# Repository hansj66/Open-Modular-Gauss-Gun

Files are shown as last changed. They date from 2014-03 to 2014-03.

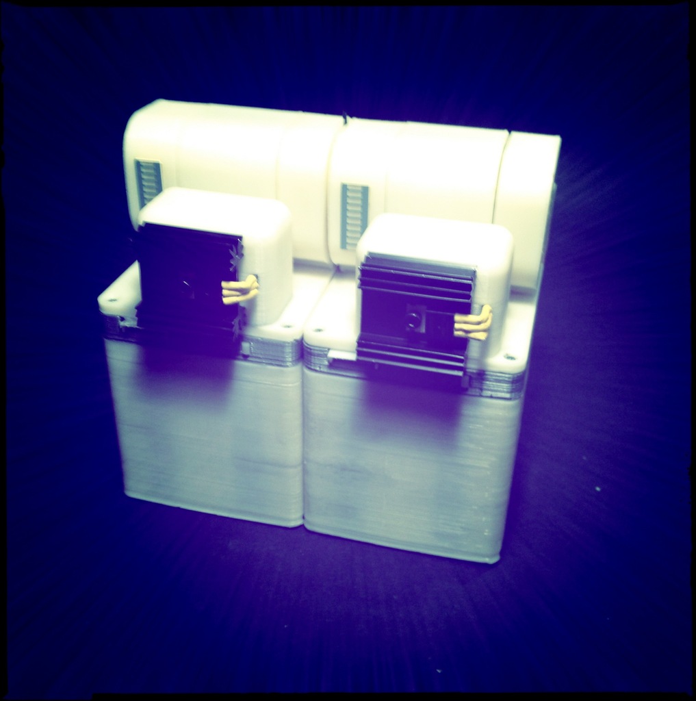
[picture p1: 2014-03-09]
Two_Stages_display_large.jpg

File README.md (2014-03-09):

Open-Modular-Gauss-Gun
======================

Description

A modular electromagnetic accelerator that actually works...;)

Warning: This project involves the use of a capacitor bank that contains more than enough energy to kill you. Do not attempt to build this unless you know what you are doing ! 
(There is a real possibility of poking an eye out or qualifying for a Darwin Award if you make a mistake...)

The inspiration to create this came from reading the books "Kristian Birkeland - The First Space Scientist" (available from Springer) and "Zero To Eighty" by Edwin Fitch Northrup.

Instructions

Each module contains a high voltage charger, an optical trigger, capacitor bank, voltage indicator, accelerator coil and switch circuitry. When the projectile interrupts an infrared beam at one end, it triggers a pulse of several hundred amps through the acceleration coil. The pulse peaks after approximately 4 ms. The projectile is then accelerated through the module. 

This is a modular design that uses optical triggers. Because of this, it is possible to stack several modules to achieve more power (each module weighs approx 1 Kg)

If you want to see the this thing in action, there is a video on YouTube: youtube.com/watch?v=KeSjeUIltcI, and on my blog: timeexpander.com/wordpress/archives/5124 (norwegian only - sorry)

Please be _very_ careful if you plan on building something like this. I am myself an amateur regarding electronics and I can make no promises or guarantees regarding the safety of the electronics or design.

Parts list is maintained in bom.txt

(The two additional schematics you will need are in the video)

PS. varying the length of the projectile can make a really big difference in kinetic energy.

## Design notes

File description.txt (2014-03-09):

Description

A modular electromagnetic accelerator that actually works...;)

Warning: This project involves the use of a capacitor bank that contains more than enough energy to kill you. Do not attempt to build this unless you know what you are doing ! 
(There is a real possibility of poking an eye out or qualifying for a Darwin Award if you make a mistake...)

The inspiration to create this came from reading the books "Kristian Birkeland - The First Space Scientist" (available from Springer) and "Zero To Eighty" by Edwin Fitch Northrup.

Instructions

Each module contains a high voltage charger, an optical trigger, capacitor bank, voltage indicator, accelerator coil and switch circuitry. When the projectile interrupts an infrared beam at one end, it triggers a pulse of several hundred amps through the acceleration coil. The pulse peaks after approximately 4 ms. The projectile is then accelerated through the module. 

This is a modular design that uses optical triggers. Because of this, it is possible to stack several modules to achieve more power (each module weighs approx 1 Kg)

If you want to see the this thing in action, there is a video on YouTube: youtube.com/watch?v=KeSjeUIltcI, and on my blog: timeexpander.com/wordpress/archives/5124 (norwegian only - sorry)

Please be _very_ careful if you plan on building something like this. I am myself an amateur regarding electronics and I can make no promises or guarantees regarding the safety of the electronics or design.

Parts list:
- thingiverse.com/thing:19687
- 12-15 V power supply / battery
- 47 ohm 0,5W resistor
- 1 kohm 0,5W resistor (2 x)
- 390 kohm 0,5W resistor
- 4 kohm 0,5W resistor
- 450V/1000uF capacitors (6 x. Maximum dimensions are 35 x 65 mm)
- LED Bargraph display
- LM3914 
- 7805 Voltage regulator
- TSAL7200 (or equivalent) IR diode
- LTR3208E (or equivalent) phototransistor
- 2N3904 small signal transistor (or equivalent) 
- 50RIA120 SCR (or equivalent). Must be able to survive a current of 7-800 A for the pulse duration (typically 8-10 ms)
- 47 ohm (5W or higher) current limiting resistor (to be mounted between the boost converter and capacitor bank)
- 450V capable switch with a 300 ohm/5W minimum current limiting resistor (to be mounted across the capacitors as a safety discharge switch. This is essential in case of a misfire. The capacitors can store a lethal charge for more than a day). The design accommodates a switch with a form factor like an arcade microswitch.
- carbon fiber tube (5 mm outer diameter). Use a dremel tool to create slots for the infrared light beam.
- approx 150 grams of 1mm insulated copper wire for the accelleration 
coil. The coil should have a series resistance of approx 0,3-0,4 ohm and an inductance of approx 190 uH (You can counterwind parts of the coil to reduce inductance if you need a higher series resistance). With these parameters the pulse should be critically damped and there will (hopefully) not be a need for additional protection circuitry.
- plastite screws (12)

(The two additional schematics you will need are in the video)

PS. varying the length of the projectile can make a really big difference in kinetic energy.

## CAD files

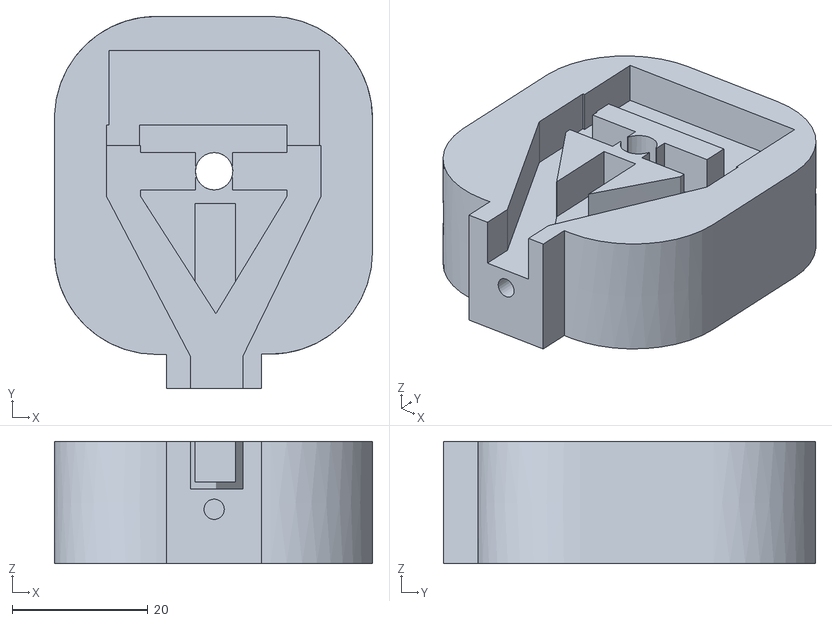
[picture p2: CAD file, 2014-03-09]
Optotrigger.stl
46.8 x 54.8 x 18.0

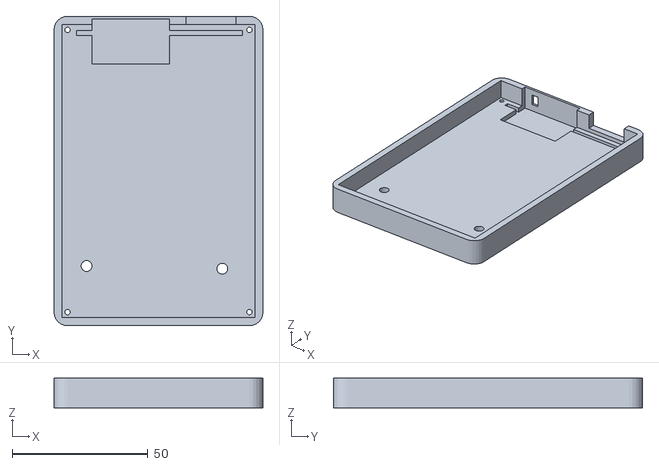
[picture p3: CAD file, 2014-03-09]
WiringBay.stl
77.0 x 114.0 x 11.0

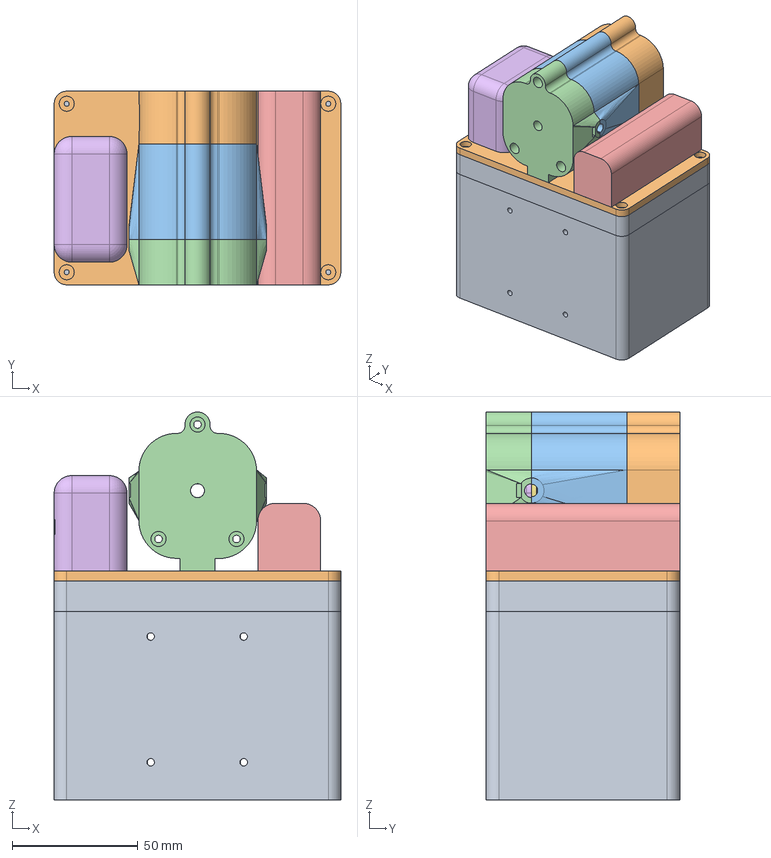
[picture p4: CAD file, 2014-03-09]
GaussGun.stp
114.0 x 77.0 x 154.3 mm
GaussGun.stp_ForBodies
Cover
Coil
Optotrigger
SCRmodule
Chargermodule
Coilbobbin
CoilEndplate
WiringBay
Voltage indicator

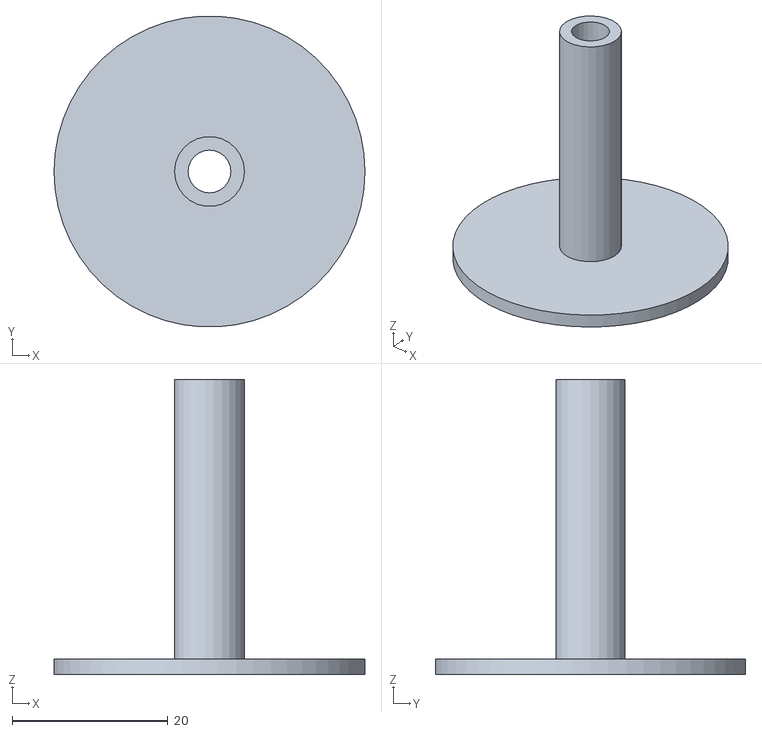
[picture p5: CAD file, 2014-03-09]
Coil_b.stl
40.0 x 39.9 x 38.0

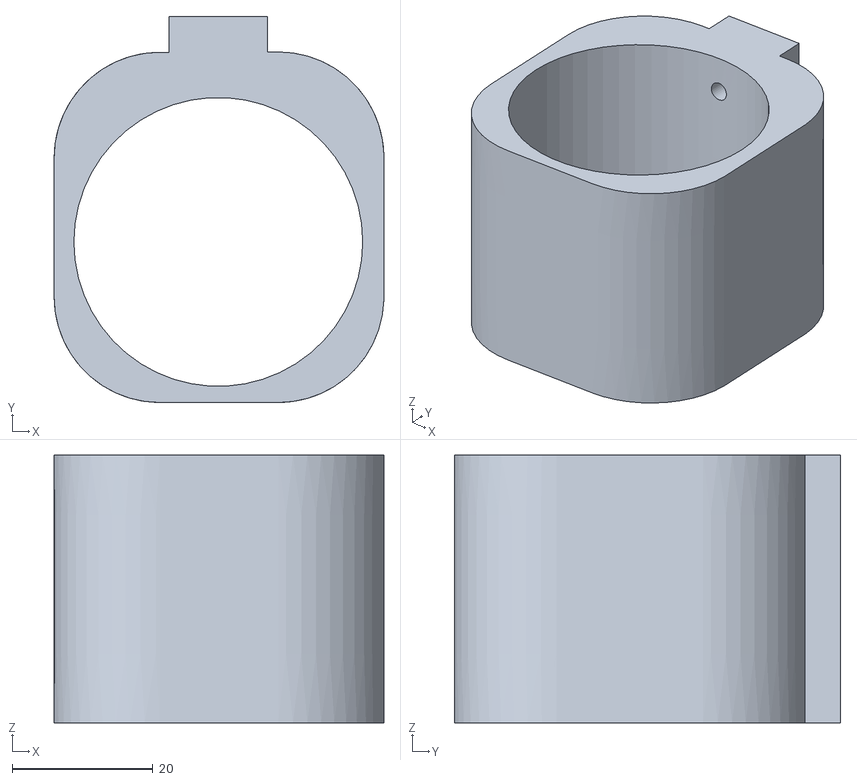
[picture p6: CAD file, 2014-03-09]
Coilsleeve.stl
46.8 x 54.8 x 38.0

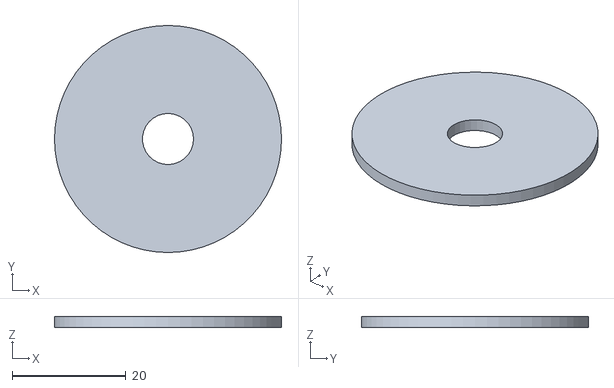
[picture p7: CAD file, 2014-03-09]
Coil_a.stl
40.0 x 40.0 x 2.00

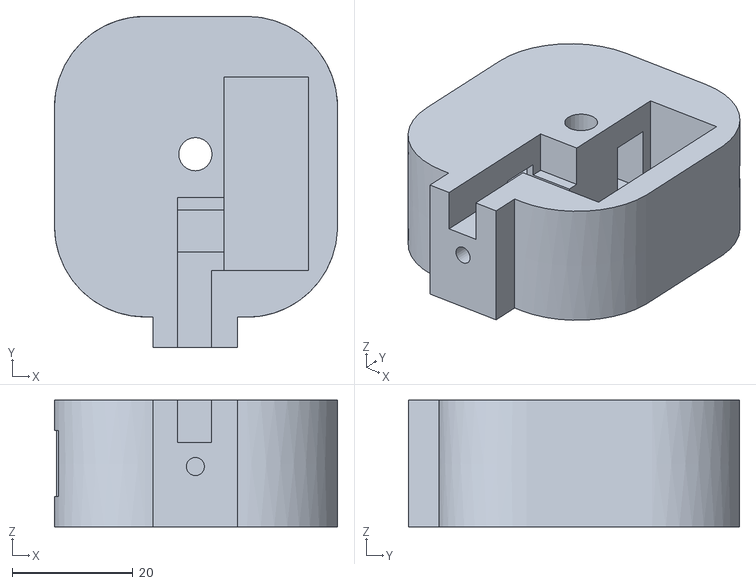
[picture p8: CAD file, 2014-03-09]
ChargeIndicator.stl
46.8 x 54.8 x 21.0

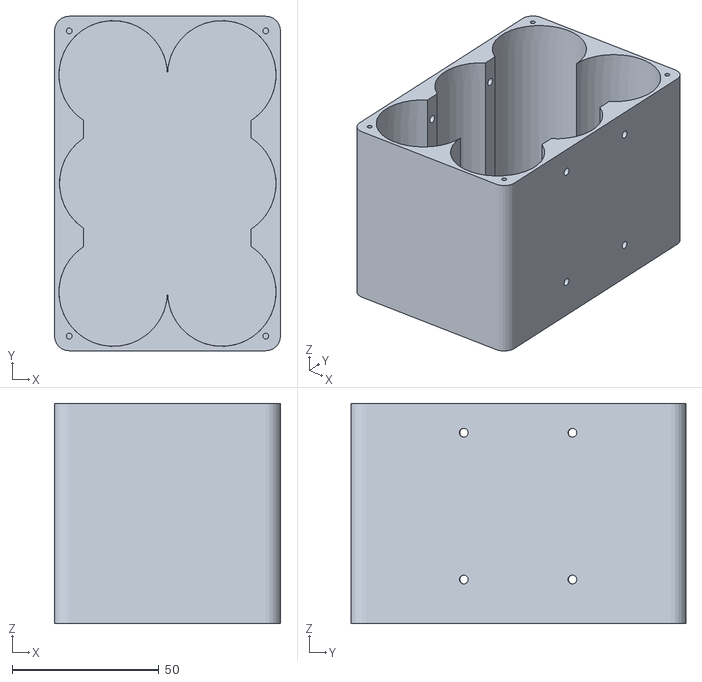
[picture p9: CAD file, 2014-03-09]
Capacitorbank.stl
77.0 x 114.0 x 75.0

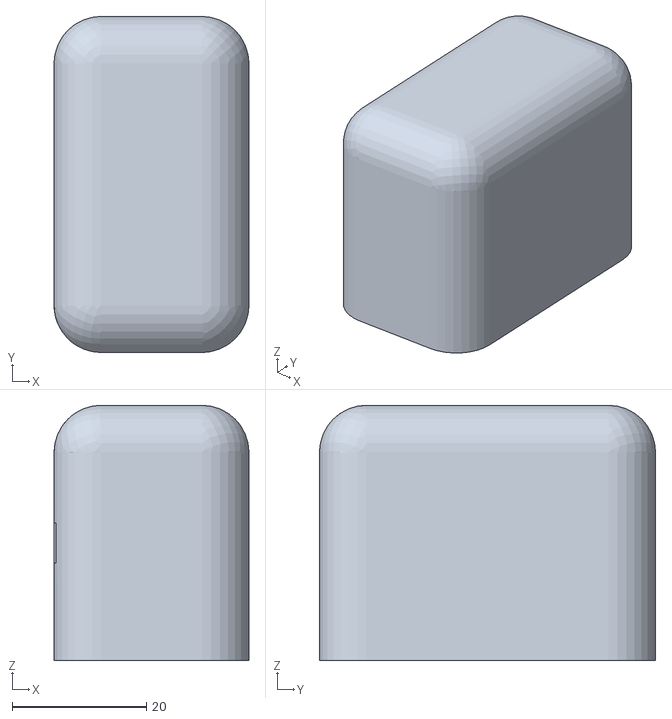
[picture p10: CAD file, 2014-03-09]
Inverter_module.stl
29.0 x 50.0 x 38.0

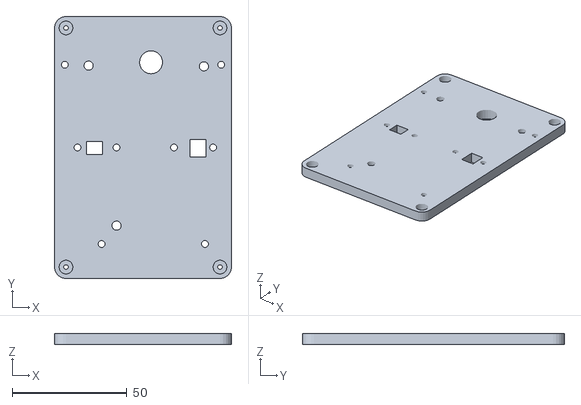
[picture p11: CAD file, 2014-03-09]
Cover.stl
77.0 x 114.0 x 5.00

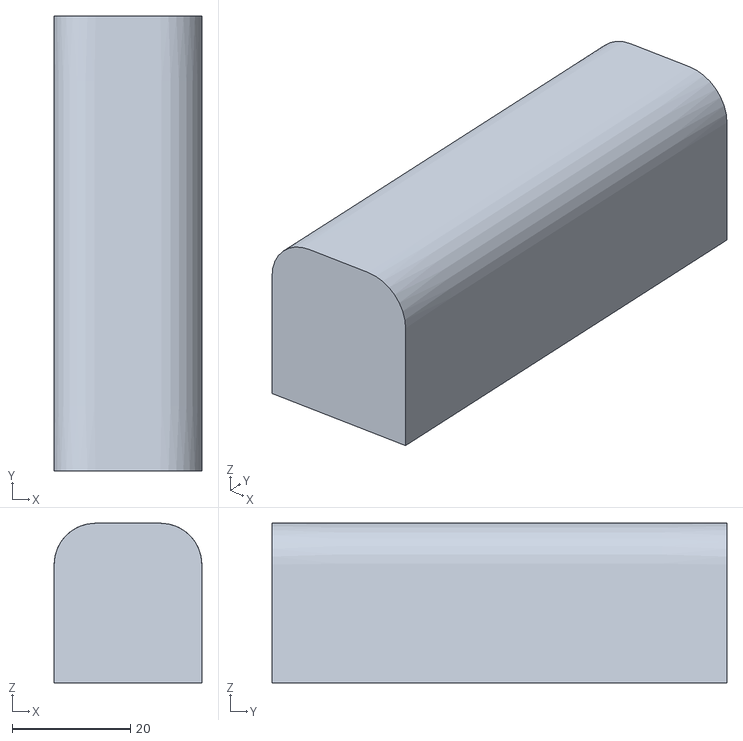
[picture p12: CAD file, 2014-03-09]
SCR_module.stl
25.0 x 77.0 x 27.0
